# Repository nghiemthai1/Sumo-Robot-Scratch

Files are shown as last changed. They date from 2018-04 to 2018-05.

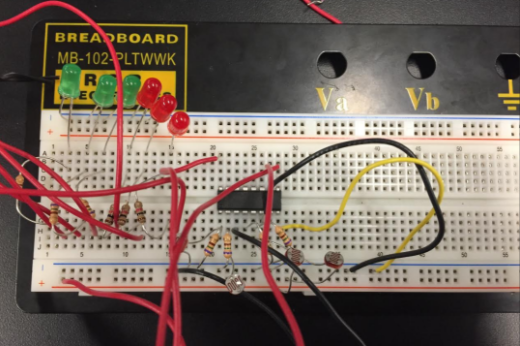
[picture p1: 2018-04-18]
Final Project Pictures/Multiplexer Schematic.png

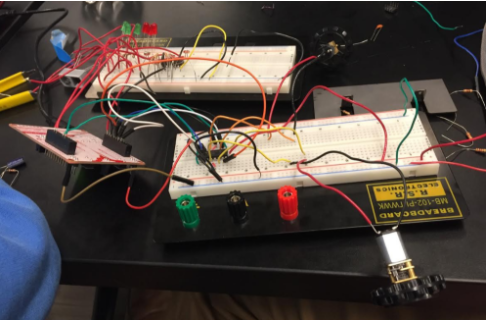
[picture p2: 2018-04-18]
Final Project Pictures/Multiplexer Schematic Overall.png

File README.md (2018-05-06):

# Sumo-Robot
### The SumoTest folder 
Contains the code for the robot. <br />
### The diptrace folder
Contains the schematic and pcb files.<br />
### The Final Project Pictures folder 
Contains figures in the final report.<br />
### The Parts List Emb.ods 
Contains a list of parts ordered, can only be opened with LibreOffice or other applications 
that can open .ods files.<br />
### The sumobot-final-project-report.pdf 
Is a pdf of - surprise- the sumobot final project report for Embedded Systems.<br />
blue

# Extra!
The sumo-bot is now implemented with a PID controller that follow an object at a desired distance!
### The PID_Controller folder contains the code and the pdf report of the project. 
Below is some graphic representation. <br />
 ezgif com-crop

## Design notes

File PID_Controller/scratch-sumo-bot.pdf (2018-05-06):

– ECE 09.321: Systems and Controls –

## Scratch Sumo-Bot: Tracking a Moving Object

Thai Nghiem, Russell Binaco Section 3

May 6, 2018

## 1 Abstract

## 2 Introduction

## 3 Standards And Constraints

Standards and constraints are regulations and limitations surrounding a project. Taking standards into consideration before designing the sumo-bot plays an important role in making the second-order design decisions and determining the success of the system.

### 3.1 Standards

Since the secondary purpose of the project is to compete in the Annual Rowan Prof Bots competition, the sumo-bot strictly follows the rules of competition. According to the rules, the design constraints of the bot are:

- The robot must have maximum dimensions of 10cm wide and 10cm long.
- The robot must have a mass no greater than 500g
- Robots must be self-impelled and self-controlled

All design choices must consider and fall within these parameters. The full competition ruleset can be found here (https://sumo.rowanieee.org/)

### 3.2 Constraints

Many minor constraints have to be taken into considerations when building this sumobot object follower, such as the stability, price, motor speed, distance, and available

Thai Nghiem, Russell Binaco | – ECE 09.321: Systems and Controls – | Section 3

hardware. First of all, the system must not have a high percent overshoot, since it might cause collision with the target object when there is a sudden change in position. Second of all, the total cost of the object follower must be relatively cheap (under 100 US Dollars), as there was very little money that was capable of being spent. Next, since the motor have a limited no-load speed of 400 RPM, the effect of the PID controller must not be too high, as it can make the bot go too slow. Lastly, it was a constraint to not use the Arduino processors in this project because it has a large library that can make the task seems trivial to implement.

## 4 Control Design

The task of following a moving object is inherently a Systems and Control task that requires feedback. The input to the system is a desired distance, so that distance must be transformed into a form that the microprocessor can use to compute motor speeds. In addition to system characterization, the PID controller should be tuned to a desired overshoot and steady-state error, as well as responsiveness. The ability of the system to reach a stable steady state should also be considered. This section of the report discusses the desired behavior of the system from a systems and control perspective, and section 6.1 discusses how the system behaved relative to these design considerations.

### 4.1 Characterizing Your System

The system is characterized by turning the distance between the robot and the target object into a digital value using the ADC converter. First, the output of the IR sensor(PRP220) was measured at varying distances from the sumo bot. The results are seen in the table in Figure 1 below.

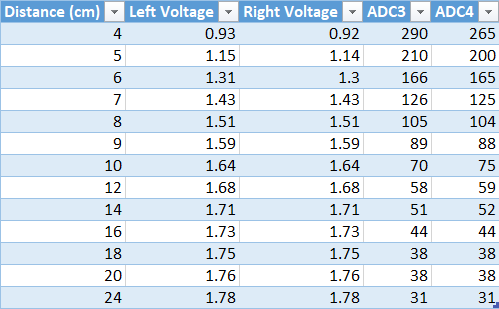
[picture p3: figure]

Figure 1: Characterization table.

Scratch Sumo-Bot: Tracking a Moving Object | 2

Thai Nghiem, Russell Binaco | – ECE 09.321: Systems and Controls – | Section 3

The results show the successful detection of an object within 30cm, a distance long enough to trail behind an object. The table is converted into a line graph as seen in Figure 2.

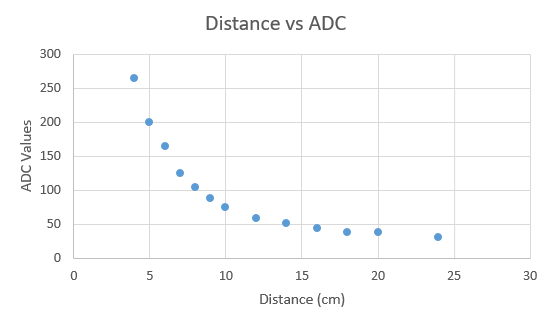
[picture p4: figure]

Figure 2: Distance vs. ADC graph.

This line is then divided into 3 pieces to create 3 piece-wise functions using equations (1) and (2) shown below. This is because an exponential decay graph is more computationally intensive to characterize than a straight line, and a piecewise function still provides a sufficient approximation of the characterized system. The implementation of the characterization code will be discussed later in Section 5.

m =

y2 − y1
x2 − x1

(1)

b = y1 − x1 · m | (2)

### 4.2 Design Goals

For a PID controller, design goals relate to the steady-state error, responsiveness (i.e. settling time) and overshoot of the system. When following an object, little to no overshoot is desired since overshoot could cause the sumo bot to collide with the object, which may not be desired. Settling time should be maximized and steady-state error should be minimized. Ultimately, the goal is to reach the desired distance from the object as quickly as possible, without overshooting that distance, and to minimize the oscillation and error at that distance.

### 4.3 Stability

By characterizing the system via the ADC readings from the sumo bot itself, the system is inherently stable. The only possible concern that could cause instability is a bad

Scratch Sumo-Bot: Tracking a Moving Object | 3

Thai Nghiem, Russell Binaco | – ECE 09.321: Systems and Controls – | Section 3

environment: for example, direct sunlight contains infrared light, which would cause the ADC readings to rise substantially and throwing off the characterization. Assuming the sumo bot is used indoors, only bad ADC readings from stray IR light or noise could cause a deviation in the system.

### 4.4 Control Loop Design

Figure 3 below shows the control loop for this system. Each portion of this loop was implemented as follows: First, the transformation from a desired distance to its equivalent ADC value was accomplished through the system characterization described above. The error signal comes from the difference between the average of the 10 most recent ADC readings and this characterized value. The implementation of the conversion from the error signal to a PWM duty cycle via the PID controller will be discussed in section 5.2. This process ultimately changes the position of the sumo bot, which is consistent with the initial set point also being a position.

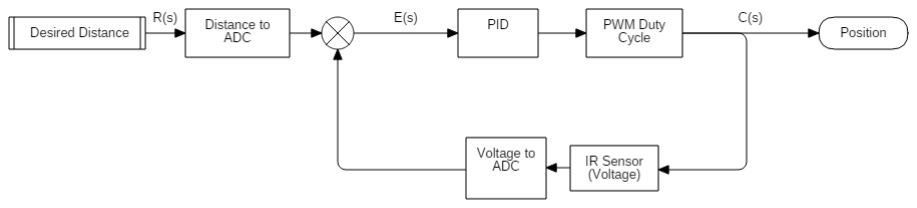
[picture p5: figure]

Figure 3: Block Diagram of PID System.

## 5 Design Discussion

### 5.1 Hardware

The sumo-bot was designed from scratch, with the advantage of being low cost, easy to adjust, and maintainable. The sumo-bot communicates with a MSP430F5529 using the built in ADC to read values from sensor and control two motors using an H-bridge. Each of the mentioned hardware parts of the robot will be discussed in detail in the following subsections.

### 5.1.1 Micro-controller

Choosing the right micro-controller was the first design choice to made, as it determines the efficiency of the system. The MSP430F5529 was decided on for various

Scratch Sumo-Bot: Tracking a Moving Object | 4

Thai Nghiem, Russell Binaco | – ECE 09.321: Systems and Controls – | Section 3

reasons. First of all, the micro-controller fits within the 10cm x 10cm dimension constraint given by the ProfBots competition. Also, the F5529 has 14 ADC channels (12 external at the device’s pins and 2 internal), which is enough for full functionality and communication with the sensors. The F5529 is also faster than most of the other boards including the G2 when making decisions off sensor readings. Finally, familiarity with the 5529 from previous projects and reusability of relevant code also played a large part in the microprocessor decision.

### 5.1.2 PCB

Three versions of the PCB was designed for the sumo-robot, but only the second version was used in the final product. In the last version, which can be seen from Figure 4 of the PCB, there are 4 main sections.

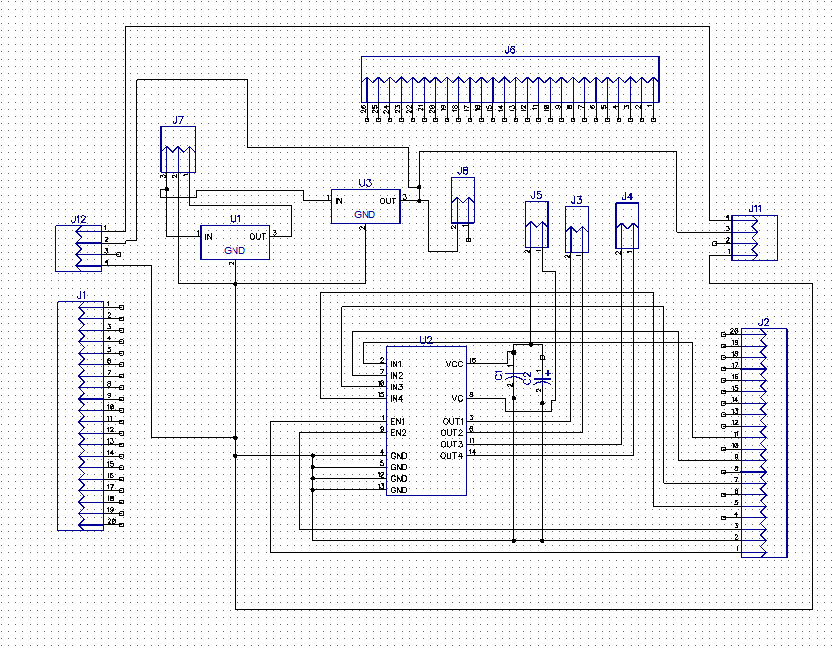
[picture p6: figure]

Figure 4: Schematic of breakout board used to power components.

The first section is the break-out board for the MSP430 to be mounted on. The second section is the H-bridge IC and the bulk and bypass capacitors that control the behavior of the 2 motors. The third section, which is on the top, is the two voltage regulators (5V and 3.3V). These are both used to supply power for the H-bridge and the MSP430. Finally, the last section, which is right next to the voltage regulator, is used for the IR sensors. In this section, the holes for the IR sensors are not connected to the pins of the MSP430, as to allow changes when actually building the robot. The layouts of the PCB can be seen in Figure 5

Scratch Sumo-Bot: Tracking a Moving Object | 5

Thai Nghiem, Russell Binaco | – ECE 09.321: Systems and Controls – | Section 3

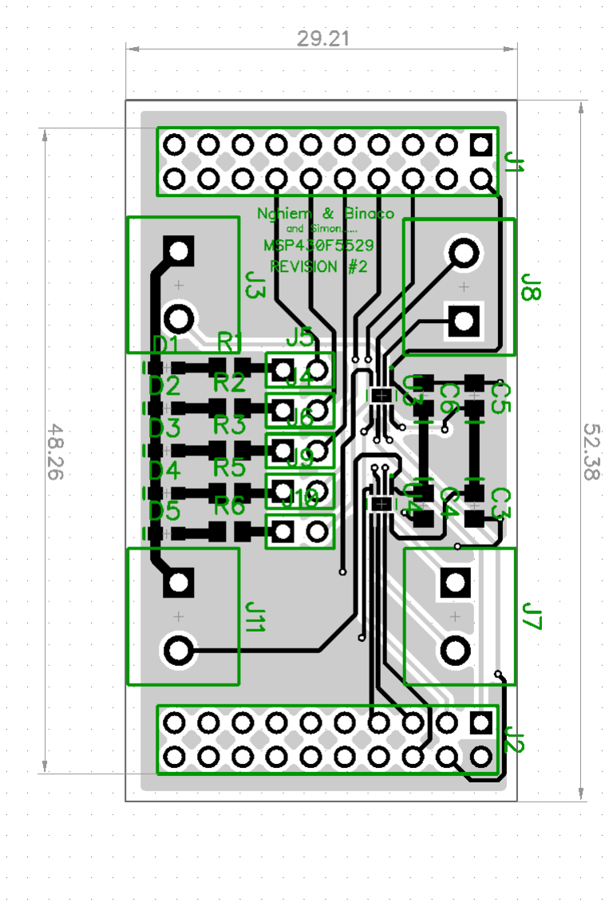
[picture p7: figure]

Figure 5: PCB Layouts of the final product.

### 5.1.3 Housing

The next step was to design the chassis and board housing in Solidworks, to be then 3-D printed. The chassiss design is based off the Zumo 32U Prime kit sumobot. The adjustments made are to optimize the specific motors chosen and adding in additional through holes for the plow and board attachment. The models are shown below in Figure 7.

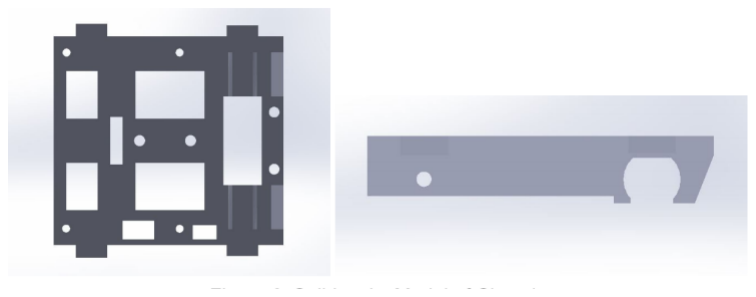
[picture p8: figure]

Figure 6: 3D Model of the Housing

Scratch Sumo-Bot: Tracking a Moving Object | 6

Thai Nghiem, Russell Binaco | – ECE 09.321: Systems and Controls – | Section 3

The next step was to take the 3-D design and import it to the Ultimaker Cura Studio to be 3-D printed. The design took approximately 8 hours to print on print speed setting of 0.1 and infill of 50

### 5.1.4 Sensors

There were many challenges when finally implementing the sensor design of the scratch sumo bot. Initially, the infrared sensor (TSSP4056) picked out needed a casing to be more accurate. However, it did not fit as well into the mechanical design of the bot, and the team was not satisfied with the performance of the TSSP4056. Upon further research of the old sumo bots used as references, the PRP220 IR sensor was discovered. The sensor was tested by the built circuit as seen in Figure ??. This circuit is then implemented in a ProtoBoard. The sensor was able to detect changes between black and white as well as objects within 30cm very well.

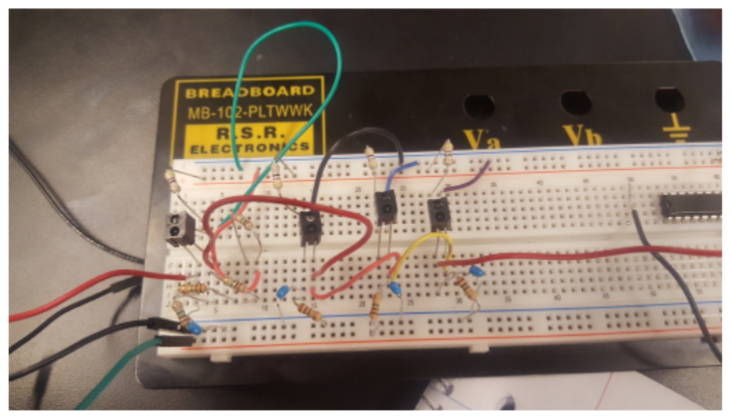
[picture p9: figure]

Figure 7: Picture of breadboard test setup with IR sensors.

### 5.1.5 Control Diagram

A general overview of the functioning of the system can be seen in Figure 8. A 12V energy sources powers a 5V regulator, a 3.3V regulator, and the motors that are connected to the H-Bridge. The 3.3V regulator powers the infrared LEDs, which reflect off surfaces and into the nearby infrared sensors. The sensors send an analog voltage back into the MSP430, which converts it into an analog signal and compares it thresholds that drive the logic of the H-bridge. Finally, the H-bridge controls the motors of the sumobot. The code is explained more in detail in the design approach.

Scratch Sumo-Bot: Tracking a Moving Object | 7

Thai Nghiem, Russell Binaco | – ECE 09.321: Systems and Controls – | Section 3

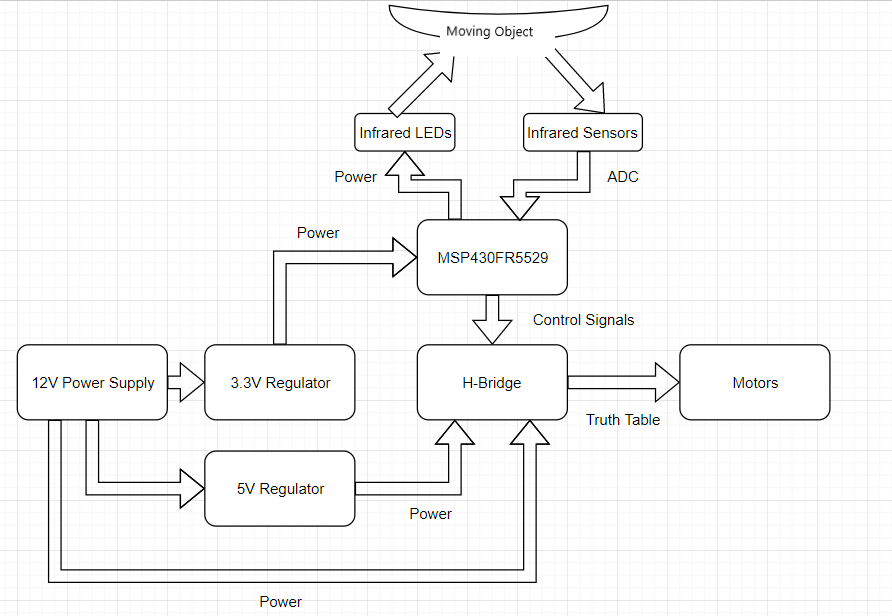
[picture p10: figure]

Figure 8: Diagram of the sumo-bot as a whole.

### 5.2 Software

### 5.2.1 ADC12

The analog to digital (ADC) conversion plays an important role in the design of the sumobot. The sensors output a voltage depending the distance of objects in front of them. The ADC interrupt was placed in a while loop so the microprocessor is constantly checking the voltage readings from the sensors in order to make decisions based on the inputs.
The code for the ADC conversion that is used in sensing the environment can be seen below (with the ADC initialization omitted).

/ ∗
∗ Enable the ADC c o n v e rt e r t o s t a r t sensing the envi ronment
∗ Thi s f u n c t i o n i s c a l l e d i n main
∗ /
v o i d sensing ( v o i d )
{
ADC12CTL0 |= ADC12ENC; | / / ADC12 enabled
ADC12CTL0 |= ADC12SC; | / / S t a r t sampling / con ve r sion
b i s S R r e g i s t e r ( GIE ) ; | / / LPM0, ADC12 ISR w i l l f o r c e e x i t

}

### 5.2.2 PWM - Motors Speed

Pulse width modulation is used to control the speed of each motor on the sumo-bot. In order for this to be achieved two PWM signals were output to Pin 1.4 and Pin 2.4.

Scratch Sumo-Bot: Tracking a Moving Object | 8

Thai Nghiem, Russell Binaco | – ECE 09.321: Systems and Controls – | Section 3

Pin 1.4 controlled the speed of the right motor and Pin 2.4 controlled the speed of the left motor. TA0CC3 was used to control the right motor and TA2CCR1 was used to control the left motor. The PWM cycle is controlled using values 0-999. Setting TA0CC3/TA2CCR1 = 0 will produce a duty cycle of 0% and setting TA0CC3/TA2CCR1 = 999 will produce a duty cycle of 100%.
The code to set the speed of motor using PWM can be seen below (with the PWM initialization being omitted).

/ ∗
∗ Thi s f u n c t i o n s et the PWM value of the
∗ two motors , hence c o n t r o l t h e i r speed ∗ /
v o i d setMoto r ( i n t l e f t , i n t r i g h t )
{
i f ( r i g h t < 0 ) / / Backwards , clo c k−wise
{
| P2OUT |= BIT5 ; / / Sets d i r e c t i o n f o r H−b r i d g e
TA0CCR3 = ( l e f t ∗ −1); / / Speed of the motor CCR/1000 }
e l s e i f ( r i g h t == 0 ) / / st o p p i n g
{
| TA0CCR3 = 0;
}
e l s e / / Forwards , counte r clo c k−wise
{
| P2OUT &= ˜ BIT5 ; / / Sets d i r e c t i o n f o r H−b r i d g e TA0CCR3 = l e f t ; / / Speed of the motor CCR/1000

}
| | [ same code i s done f o r the l e f t ]

}

### 5.2.3 Characterization

As previously discussed, the distance between the sumo-bot and the target object is characterized into ADC value as to control the PWM of the 2 motors. This is done by turning the line graph in Figure 2 into 3 straight line graphs, as shown in Figure 9. The first graph represents the ADC value versus a distance from 0 to 7 cm. The second graph represents the ADC value versus a distance from 7 to 12 cm. The last graph represents the ADC value versus a distance from 12 to 30 cm.

Scratch Sumo-Bot: Tracking a Moving Object | 9

Thai Nghiem, Russell Binaco | – ECE 09.321: Systems and Controls – | Section 3

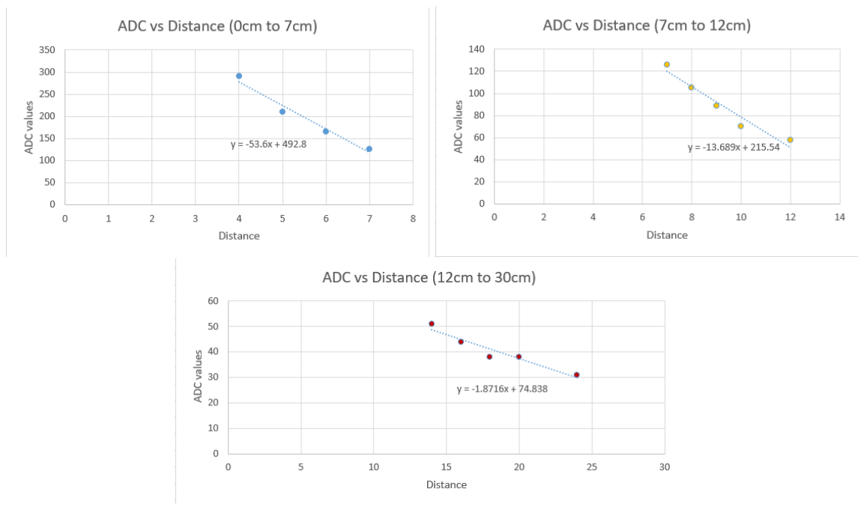
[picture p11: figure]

Figure 9: 3 straight line graphs derived from 1 curved line.

These graphs are then utilized to create 3 piecewise functions using Equation (1) and (2). The 3 functions is implemented in the code as follows to give us the equivalent ADC values.

/ ∗
∗ C h a r a ct e r i z at i o n code f o r the system
∗ Conve rt the d e s i r e d d i st a n c e t o ADC value ∗ Using piece−wise f u n c t i o n s
∗ /
v o i d distToADC ( i n t d i st a n c e ){
/ / 0cm t o 7cm range
i f ( d i st a n c e >= 0 && d i st a n c e <= 7 ){
ad c out = d i st a n c e ∗−53.6 + 4 9 2. 8;
/ / 7cm t o 12cm range
} e l s e i f ( d i st a n c e > 7 && d i st a n c e <= 12 ){ ad c out = d i st a n c e ∗−13.689 + 215.54;
/ / 12cm t o 30cm range
} e l s e i f ( d i st a n c e > 12 && d i st a n c e <= 30 ){ ad c out = d i st a n c e ∗−1.8716 + 74.838;
}
/ / D ef a u lt value
e l s e {
ad c out = 290;
}
}
Scratch Sumo-Bot: Tracking a Moving Object | 10

Thai Nghiem, Russell Binaco | – ECE 09.321: Systems and Controls – | Section 3

Hence, when the user input a desired distance of 5 cm after the target object, the above function will assign it into the first if-statement, and produce an equivalent ADC value that will control the speed of the 2 motors.

### 5.2.4 PID Controller

/ ∗
∗ P r o p o r t i o n a l − I n t e g r a l − D e r i v a t i v e C o n t r o l l e r of the r o b ot ∗ I s c a l l e d i n the I n t e r r u p t
∗ /
v o i d updatePID ( v o i d ){
/ / C a l c u l at i n g the E r r o r term
e r r o r 3P r e v = e r r o r 3 ; / / R ight motor e r r o r 4P r e v = e r r o r 4 ; / / L e f t motor e r r o r 3 = d e s i r e d − adc3 ;
e r r o r 4 = d e s i r e d − adc4 ;

/ / C a l c u l at i n g the P r o p o r t i o n a l term
p r o p o r t i o n a l 3 = Kp ∗ e r r o r 3 ; / / R ight motor p r o p o r t i o n a l 4 = Kp ∗ e r r o r 4 ; / / L e f t motor

/ / C a l c u l at i n g the D e r i v a t i v e term
d e r i v a t i v e 3 = Kd ∗ ( e r ro r3P re v−e r r o r 3 ) ; / / R ight motor d e r i v a t i v e 4 = Kd ∗ ( e r ro r4P re v−e r r o r 4 ) ; / / Ledt motor

/ / C a l c u l at i n g the accumulato r f o r the E r r o r term accumulato r3 = accumulato r3 += e r r o r 3 ;
accumulato r4 = accumulato r4 += e r r o r 4 ;

/ / Capping accumulato r value s
i f ( accumulato r3 >50){ / / R ight motor
| accumulato r3 = 50;
} e l s e i f ( accumulato r3 <−50){
| accumulato r3 = −50;
}
i f ( accumulato r4 >50){ | / / L e f t motor
| accumulato r4 = 50;
} e l s e i f ( accumulato r4 <−50){
| accumulato r4 = −50;
}

/ / C a l c u l at i n g the I n t e g r a l term
i n t e g r a l 3 = Ki ∗ accumulato r3 ; / / R ight motor i n t e g r a l 4 = Ki ∗ accumulato r4 ; / / L e f t motor
Scratch Sumo-Bot: Tracking a Moving Object | 11

Thai Nghiem, Russell Binaco | – ECE 09.321: Systems and Controls – | Section 3

/ / Adding the P r o p o r t i o n a l − I n t e g r a l − D e r i v a t i v e temrs / / up t o c r e at e the PID c o n t r o l l e r
pid3 = p r o p o r t i o n a l 3 + i n t e g r a l 3 −d e r i v a t i v e 3 ;
pid4 = p r o p o r t i o n a l 4 + i n t e g r a l 4 −d e r i v a t i v e 4 ;

/ / c o n v e rt p i d range t o PWM range setScaledMoto r ( pid3 , pid4 ) ;
}

## 6 Results and Conclusions

### 6.1 System Behavior

### 6.1.1 Proportional Control

### 6.1.2 PID Control

### 6.1.3 Steady State

### 6.2 Conclusions

### 6.3 Contributions

The team always work together through the process of making the sumo-bot object follower. However, each member has his own specialty and can be breakdown into different categories and be seen in the following table.

Thai Nghiem | Russell Binaco
Project Proposal Hardware Implementation Characterization | PID Controller Research Software Implementation Battery Sponsor

Acknowledgement: The authors would like to thank Dr. Al-Quzwini, Russell Trafford and Simonas Bublis for giving us advice and support throughout the project.

Scratch Sumo-Bot: Tracking a Moving Object | 12

Thai Nghiem, Russell Binaco | – ECE 09.321: Systems and Controls – | Section 3

## 7 Appendix A

## References

[1] Nise, Norman S. Control Systems Engineering. Wiley, 2011. Print.

## 8 Appendix B

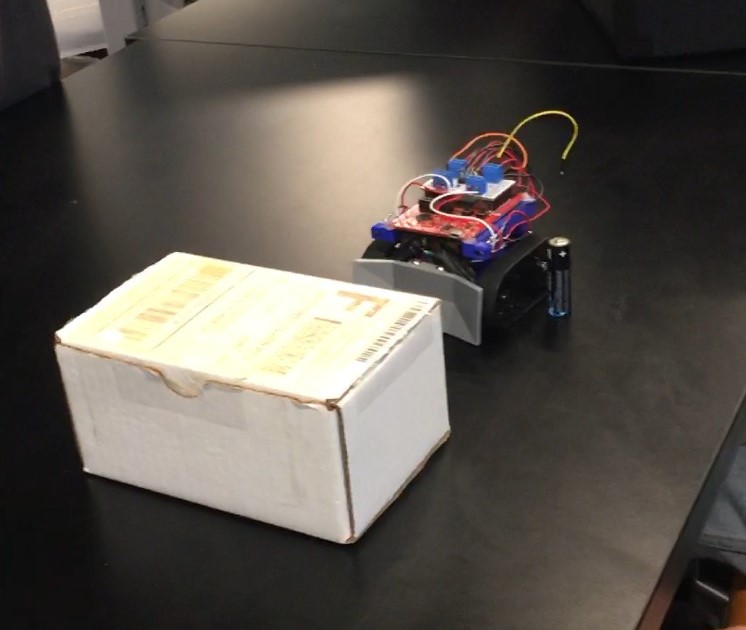
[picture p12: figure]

Figure 10: Sumo-bot and its object

Scratch Sumo-Bot: Tracking a Moving Object | 13

Thai Nghiem, Russell Binaco | – ECE 09.321: Systems and Controls – | Section 3

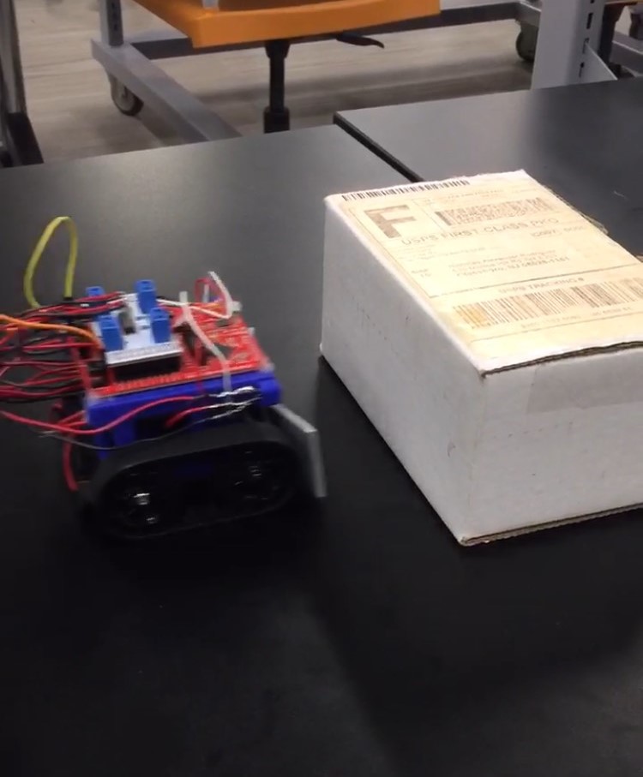
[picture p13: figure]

Figure 11: Sumo-bot and its object.

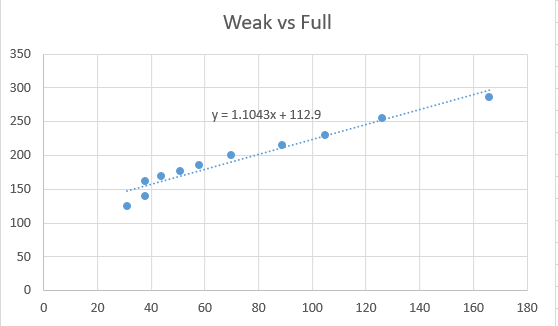
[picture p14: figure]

Figure 12: ADC value between low battery and full battery.

Scratch Sumo-Bot: Tracking a Moving Object | 14

Thai Nghiem, Russell Binaco | – ECE 09.321: Systems and Controls – | Section 3
1 | # i n c l u d e <msp430 . h>
2 | / / f o r a ve raging ADC value s
3 | i n t adc3 = 0;
4 | i n t adc4 = 0;
5 | i n t buf3 [ 1 0 ] ;
6 | i n t buf4 [ 1 0 ] ;
7 | unsigned i n t inde x ;

8
9 | i n t Kp=3;
10 | i n t Kd=0;
11 | i n t Ki =0;
12 | i n t e r r o r 3 = 0;
13 | i n t e r r o r 4 = 0;
14 | i n t e r r o r 3P r e v = 0;
15 | i n t e r r o r 4P r e v = 0;
16 | i n t p r o p o r t i o n a l 3 = 0;
17 | i n t p r o p o r t i o n a l 4 = 0;
18 | i n t d e r i v a t i v e 3 = 0;
19 | i n t d e r i v a t i v e 4 = 0;
20 | i n t accumulato r3 = 0;
21 | i n t accumulato r4 = 0;
22 | i n t i n t e g r a l 3 = 0;
23 | i n t i n t e g r a l 4 = 0;
24 | i n t pid3 = 0;
25 | i n t pid4 = 0;
26 | i n t tempLeft = 0;
27 | i n t tempRight = 0;
28 | i n t ad c out =0;
29 | i n t s c a l e v a l u e = 8;

30
31 | i n t c o n t r o l t y p e = 0;
32 | i n t f l a g = 0;
33 | i n t d e s i r e d = 0; / /ADC value
34 | v o i d PWMInit ( v o i d ) ;
35 | v o i d sensing ( v o i d ) ;
36 | v o i d s t a r t i n g ( v o i d ) ;
37 | v o i d setMoto r ( ) ;
38 | v o i d ADCInit ( v o i d ) ;
39 | v o i d updatePID ( v o i d ) ;
40 | v o i d distToADC ( i n t d i st a n c e ) ;
41 | v o i d setScaledMoto r ( i n t l e f t , i n t r i g h t ) ;
42 | v o i d p i n I n i t ( v o i d ) ;

43

44
45 | /∗ ∗
46 | ∗ main . c
47 | ∗/
48 | i n t main ( v o i d )
49 | {
50 | / / Stop watchdog t im e r
51 | WDTCTL = WDTPW | WDTHOLD;

52
53 | / / I n i t i a l i z a t i o n
54 | p i n I n i t ( ) ;
55 | PWMInit ( ) ;
56 | ADCInit ( ) ;

57

Scratch Sumo-Bot: Tracking a Moving Object | 15

Thai Nghiem, Russell Binaco | – ECE 09.321: Systems and Controls – | Section 3
58 | / / Reset the speed of both motors
59 | setMoto r ( 0 , 0 ) ;

60
61 | /∗
62 | ∗ | Compute d e s i r e d value i n ADC
63 | ∗ | Max : 200 ( c l o s e st )
64 | ∗ | Min : 100 ( f u r t h e s t
65 | ∗
66 | ∗ | d e s i r e d = 200;
67 | ∗/

68
69 | / / Desi red t r a i l i n g d i st a n c e
70 | i n t d i st a n c e = 5; / / i n c e nt im et e r s
71 | distToADC ( d i st a n c e ) ; / / Di stan ce t o ADC value

72
73 | / / Sumo−bot c o n st a nt l y sense the envi ronment
74 | w h i l e ( 1 ) / / i n i f i t e loop
75 | {
76 | sensing ( ) ;
77 | }
78 | }

79

80
81 | v o i d s t a r t i n g ( v o i d )
82 | {
83 | sensing ( ) ;
84 | }

85
86 | /∗
87 | ∗ Enable the ADC c o n v e rt e r t o s t a r t sensing the envi ronment
88 | ∗ Thi s f u n c t i o n i s c a l l e d i n main
89 | ∗/
90 | v o i d sensing ( v o i d )
91 | {
92 | ADC12CTL0 |= ADC12ENC; | / / ADC12 enabled
93 | ADC12CTL0 |= ADC12SC; | / / S t a r t sampling / con ve r sion
94 | b i s S R r e g i s t e r ( GIE ) ; | / / LPM0, ADC12 ISR w i l l f o r c e e x i t

95
96 }

97
98 | /∗
99 | ∗ P r o p o r t i o n a l − I n t e g r a l − D e r i v a t i v e C o n t r o l l e r of the r o b ot
100 | ∗ I s c a l l e d i n the I n t e r r u p t
101 | ∗/
102 | v o i d updatePID ( v o i d ) {
103 | / / C a l c u l at i n g the E r r o r term
104 | e r r o r 3P r e v = e r r o r 3 ; / / R ight motor
105 | e r r o r 4P r e v = e r r o r 4 ; / / L e f t motor
106 | e r r o r 3 = d e s i r e d − adc3 ;
107 | e r r o r 4 = d e s i r e d − adc4 ;

108
109 | / / C a l c u l at i n g the P r o p o r t i o n a l term
110 | p r o p o r t i o n a l 3 = Kp ∗ e r r o r 3 ; / / R ight motor
111 | p r o p o r t i o n a l 4 = Kp ∗ e r r o r 4 ; / / L e f t motor

112
113 | / / C a l c u l at i n g the D e r i v a t i v e term
114 | d e r i v a t i v e 3 = Kd ∗ ( e r ro r3P re v−e r r o r 3 ) ; / / R ight motor
Scratch Sumo-Bot: Tracking a Moving Object | 16

Thai Nghiem, Russell Binaco | – ECE 09.321: Systems and Controls – | Section 3
115 | d e r i v a t i v e 4 = Kd ∗ ( e r ro r4P re v−e r r o r 4 ) ; / / Ledt motor

116
117 | / / C a l c u l at i n g the accumulato r f o r the E r r o r term
118 | accumulato r3 = accumulato r3 += e r r o r 3 ;
119 | accumulato r4 = accumulato r4 += e r r o r 4 ;

120
121 | / / Capping accumulato r value s
122 | i f ( accumulato r3 >50){ / / R ight motor
123 | accumulato r3 = 50;
124 | } e l s e i f ( accumulato r3 <−50){
125 | accumulato r3 = −50;
126 | }

127
128 | i f ( accumulato r4 >50){ | / / L e f t motor
129 | accumulato r4 = 50;
130 | } e l s e i f ( accumulato r4 <−50){
131 | accumulato r4 = −50;
132 | }

133
134 | / / C a l c u l at i n g the I n t e g r a l term
135 | i n t e g r a l 3 = Ki ∗ accumulato r3 ; / / R ight motor
136 | i n t e g r a l 4 = Ki ∗ accumulato r4 ; / / L e f t motor

137
138 | / / Adding the P r o p o r t i o n a l − I n t e g r a l − D e r i v a t i v e temrs
139 | / / up t o c r e at e the PID c o n t r o l l e r
140 | pid3 = p r o p o r t i o n a l 3 + i n t e g r a l 3 −d e r i v a t i v e 3 ;
141 | pid4 = p r o p o r t i o n a l 4 + i n t e g r a l 4 −d e r i v a t i v e 4 ;

142
143 | / / c o n v e rt p i d range t o PWM range
144 | setScaledMoto r ( pid3 , pid4 ) ;
145 | }

146
147 | /∗
148 | ∗ Thi s f u n c t i o n s ca le the PWM range , s in ce the l e f t motor i s
149 | ∗ s l i g h t l y st r o n g e r than the r i g h t motor , making the r o b ot
150 | ∗ st e e r r i g h t .
151 | ∗/
152 | v o i d setScaledMoto r ( i n t l e f t , i n t r i g h t ) {
153 | / / l e f t l i m i t −999 t o 999
154 | / / r i g h t l i m i t −870 t o 870
155 | / / expected range −200 t o 200
156 | tempLeft = ( l e f t ∗5/ 2 ) ∗ s c a l e v a l u e ;
157 | tempRight = ( ( r i g h t ∗9 ) / 4 ) ∗ s c a l e v a l u e ;

158
159 | / / 30 i s minimum value ( f u r t h e s t )
160 | i f ( tempLeft < 30 && tempLeft > 0 ) {
161 | tempLeft = 30;
162 | }
163 | i f ( tempRight < 30 && tempRight > 0 ) {
164 | tempRight = 30;
165 | }

166
167 | i f ( tempLeft > −30 && tempLeft < 0 ) {
168 | tempLeft = −30;
169 | }
170 | i f ( tempRight > −30 && tempRight < 0 ) {
171 | tempRight = −30;
Scratch Sumo-Bot: Tracking a Moving Object | 17

Thai Nghiem, Russell Binaco | – ECE 09.321: Systems and Controls – | Section 3
172 | }
173 | / / 999 i s maximum value ( c l o s e st )
174 | i f ( tempLeft< −999){
175 | | tempLeft = −999;
176 | }
177 | i f ( tempRight< −999){
178 | tempRight = −999;
179 | }

180
181 | i f ( tempLeft >999){
182 | | tempLeft = 999;
183 | }
184 | i f ( tempRight >870){
185 | | tempRight = 870;
186 | }
187 | / / | R ight | L e f t
188 | setMoto r ( tempLeft , tempRight ) ;

189
190 }

191
192 | /∗
193 | ∗ Thi s f u n c t i o n s et the PWM value of the
194 | ∗ two motors , hence c o n t r o l t h e i r speed
195 | ∗/
196 | v o i d setMoto r ( i n t l e f t , i n t r i g h t )
197 | {
198 | i f ( r i g h t < 0 ) / / Backwards , clo c k−wise
199 | {
200 | P2OUT |= BIT5 ; / / Sets d i r e c t i o n f o r H−b r i d g e
201 | TA0CCR3 = ( l e f t ∗ −1) ; / / Speed of the motor CCR/1000
202 | }
203 | e l s e i f ( r i g h t == 0 ) / / st o p p i n g
204 | {
205 | | TA0CCR3 = 0;
206 | }
207 | e l s e / / Forwards , counte r clo c k−wise
208 | {
209 | P2OUT &= ˜ BIT5 ; / / Sets d i r e c t i o n f o r H−b r i d g e
210 | TA0CCR3 = l e f t ; / / Speed of the motor CCR/1000
211 | }

212
213 | i f ( l e f t < 0 )
214 | {
215 | | P1OUT |= BIT5 ;
216 | TA2CCR1 = ( r i g h t ∗ −1) ;
217 | }
218 | e l s e i f ( l e f t == 0 )
219 | {
220 | | TA2CCR1 = 0;
221 | }
222 | e l s e / / fo rwa rds , clo c k−wise
223 | {
224 | | P1OUT &= ˜ BIT5 ;
225 | | TA2CCR1 = r i g h t ;
226 | }
227 | }

228

Scratch Sumo-Bot: Tracking a Moving Object | 18

Thai Nghiem, Russell Binaco | – ECE 09.321: Systems and Controls – | Section 3
229 | /∗
230 | ∗ C h a r a ct e r i z at i o n code f o r the system
231 | ∗ Conve rt the d e s i r e d d i st a n c e t o ADC value
232 | ∗ Using piece−wise f u n c t i o n s
233 | ∗/
234 | v o i d distToADC ( i n t d i st a n c e ) {
235 | / / 0cm t o 7cm range
236 | i f ( d i st a n c e >= 0 && d i st a n c e <= 7 ) {
237 | ad c out = d i st a n c e ∗−53.6 + 4 9 2. 8;
238 | / / 7cm t o 12cm range
239 | } e l s e i f ( d i st a n c e > 7 && d i st a n c e <= 12 ){
240 | ad c out = d i st a n c e ∗−13.689 + 215.54;
241 | / / 12cm t o 30cm range
242 | } e l s e i f ( d i st a n c e > 12 && d i st a n c e | <= 30 ){
243 | ad c out = d i st a n c e ∗−1.8716 + 74.838;
244 | }
245 | / / D ef a u lt value
246 | e l s e {
247 | ad c out = 290;
248 | }
249 | }
250 | v o i d p i n I n i t ( v o i d ) {
251 | P2DIR |= BIT0 ; | / / Pin 2.0 i n i t i a l i z a t i o n
252 | P2OUT |= BIT0 ;

253
254 | P2DIR |= BIT2 ; | / / Pin 2.2 i n i t i a l i z a t i o n
255 | P2OUT |= BIT2 ;

256
257 | P2DIR |= BIT5 ;
258 | P1DIR |= BIT5 ;

259
260 | P1SEL =0; / / S e l e ct GPIO o pt i o n
261 | P1DIR |= BIT0 ; / / s et P o rt 1.0 o ut p ut −−−LED
262 | P1OUT &= ˜ BIT0 ; | / / LED OFF

263
264 | P4SEL =0; / / S e l e ct GPIO o pt i o n
265 | P4DIR |= BIT7 ; / / s et P o rt 4.7 o ut p ut −−−LED
266 | P4OUT &= ˜ BIT7 ; | / / LED OFF

267
268 | P1DIR &= ˜ ( BIT1 ) ; / / s et P o rt 1.1 i n p ut −−− pushbutton
269 | P1REN|= BIT1 ; / / enable p u l l −up / p u l l −down r e s i s t o r on
270 | P1OUT|= BIT1 ; / / choose the p u l l −up r e s i s t o r

271
272 | P1IE |= BIT1 ; / / enable the i n t e r r u p t on P o rt 1.1
273 | P1IES |= BIT1 ; / / s et as f a l l i n g edge
274 | P1IFG &= ˜ ( BIT1 ) ; / / c l e a r i n t e r r u p t f l a g
275 | }
276 | v o i d PWMInit ( v o i d )
277 | {
278 | P1DIR |= BIT4 ; | / / I n i t i a l i z e PWM t o o ut p ut on P1. 4
279 | P1SEL |= BIT4 ;

280
281 | P2DIR |= BIT4 ; | / / I n i t i a l i z e PWM t o o ut p ut on P2. 4
282 | P2SEL |= BIT4 ;

283
284 | TA0CCR0 =1000−1;
285 | TA2CCR0 =1000−1;
Scratch Sumo-Bot: Tracking a Moving Object | 19

Thai Nghiem, Russell Binaco | – ECE 09.321: Systems and Controls – | Section 3
286 | TA0CCTL3 =OUTMOD 7;
287 | TA0CCR3 =999;
288 | TA2CCTL1 =OUTMOD 7;
289 | TA2CCR1 = 999;
290 | TA0CTL = TASSEL 2 + MC 1 + TACLR;
291 | TA2CTL = TASSEL 2 + MC 1 + TACLR;
292 | }

293
294 | v o i d ADCInit ( v o i d )
295 | {
296 | ADC12CTL0 = ADC12ON+ADC12MSC+ADC12SHT02; / / Turn on ADC12, s et sampling
time
297 | ADC12CTL1 = ADC12SHP+ADC12CONSEQ 1; | / / Use sampling t ime r , s i n g l e
sequence
298 | ADC12MCTL0 = ADC12INCH 0 ; | / / r e f +=AVcc , channel = A0
299 | ADC12MCTL1 = ADC12INCH 1 ; | / / r e f +=AVcc , channel = A1
300 | ADC12MCTL2 = ADC12INCH 2 ; | / / r e f +=AVcc , channel = A2
301 | ADC12MCTL3 = ADC12INCH 3 ;
302 | ADC12MCTL4 = ADC12INCH 4 + ADC12EOS; | / / r e f +=AVcc , channel = A3 ,
end seq .
303 | ADC12IE = 0x10 ; | / / Enable ADC12IFG. 3
304 | ADC12CTL0 |= ADC12ENC; | / / Enable con ve r sion s
305 | /∗ Sets ADC Pin t o NOT GPIO∗/
306 | P6SEL |= BIT1 + BIT2 + BIT3 + BIT4 ; | / / P6. 0 ADC
o pt i o n s e l e c t
307 | P6DIR &= ˜ ( BIT1 + BIT2 + BIT3 + BIT4 ) ;
308 | P6REN |= BIT1 + BIT2 + BIT3 + BIT4 ;
309 | P6OUT &= ˜ ( BIT1 + BIT2 + BIT3 + BIT4 ) ;
310 | ADC12CTL0 |= ADC12ENC;
311 | ADC12CTL0 |= ADC12SC;
312 | }

313
314 | # i f d ef i n e d ( TI COMPILER VERSION ) | | d ef i n e d ( IAR SYSTEMS ICC )
315 | #pragma v e ct o r = ADC12 VECTOR
316 | i n t e r r u p t v o i d ADC12 ISR ( v o i d )
317 | # e l i f d ef i n e d ( GNUC )
318 | v o i d | a t t r i b u t e | ( ( i n t e r r u p t (ADC12 VECTOR ) ) ) ADC12 ISR ( v o i d )
319 | #e l s e
320 | # e r r o r Compile r not suppo rted !
321 | # e n d if
322 | {

323
324 | sw it c h ( | e v e n i n r a n g e ( ADC12IV , 3 4 ) )
325 | {
326 | case | 0: break ; | / / Ve cto r | 0: | No i n t e r r u p t
327 | case | 2: break ; | / / Ve cto r | 2: | ADC o v e rf l ow
328 | case | 4: break ; | / / Ve cto r | 4: | ADC t im i n g
o v e rf l ow
329 | case | 6: break ; | / / Ve cto r | 6: | ADC12IFG0
330 | case | 8: break ; | / / Ve cto r | 8: | ADC12IFG1
331 | case 10: break ; | / / Ve cto r 10: | ADC12IFG2
332 | case 12: break ; | / / Ve cto r 12: | ADC12IFG3
333 | case 14:
334 | / / For eve ry 10 ADC samples , we use 1 f o r s t a b i l i t y of the system
335 | i f ( inde x < 10 ){ | / / adds new value t o a r r a y f o r average of 10
336 | buf3 [ inde x ] = ADC12MEM3; / / b u f f e r f o r r i g h t motor
337 | buf4 [ inde x ] = ADC12MEM4;
Scratch Sumo-Bot: Tracking a Moving Object | 20

Thai Nghiem, Russell Binaco | – ECE 09.321: Systems and Controls – | Section 3
338 | inde x ++;
339 | }
340 | e l s e { | / / computes average of 10 and t r a n sm it s value ; r e s et s a r r a y
inde x
341 | long average3 = 0;
342 | long average4 = 0;
343 | i n t i = 0;
344 | f o r ( i = 0; i < 10 ; i ++){
345 | average3 += buf3 [ i ] ;
346 | average4 += buf4 [ i ] ;
347 | }
348 | average3 /= 10;
349 | average4 /= 10;
350 | inde x =0;
351 | f l a g =1;
352 | / / −120 f o r F u l l vs Weak
353 | adc3 = average3 ; / / changes dut y c y c l e
354 | adc4 = average4 ; / / changes dut y c y c l e

355
356 | / / C a l l i n g the PID c o n t r o l l e r f u n c t i o n
357 | updatePID ( ) ;
358 | }

359
360 | b i c S R r e g i s t e r o n e x i t ( LPM0 bits ) ;
361 | break ; | / / Ve cto r 14: | ADC12IFG4
362 | case 16: break ; | / / Ve cto r 16: | ADC12IFG5
363 | case 18: break ; | / / Ve cto r 18: | ADC12IFG6
364 | case 20: break ; | / / Ve cto r 20: | ADC12IFG7
365 | case 22: break ; | / / Ve cto r 22: | ADC12IFG8
366 | case 24: break ; | / / Ve cto r 24: | ADC12IFG9
367 | case 26: break ; | / / Ve cto r 26: | ADC12IFG10
368 | case 28: break ; | / / Ve cto r 28: | ADC12IFG11
369 | case 30: break ; | / / Ve cto r 30: | ADC12IFG12
370 | case 32: break ; | / / Ve cto r 32: | ADC12IFG13
371 | case 34: break ; | / / Ve cto r 34: | ADC12IFG14
372 | d e f a u l t : b reak ;
373 | }
374 | }

375
376 | /∗
377 | ∗ Button I n t e r r u p t t h a t c o n t r o l the C o n t r o l l e r Type of the r o b ot
378 | ∗ There a re 4 modes i n t o t a l : o n l y P r o p o rt i o n a l , P r o p o rt i o n a l −I n t e g r a l ,
379 | ∗ P r o p o rt i o n a l −D e r i v at i v e , and a l l P r o p o rt i o n a l −I n t e g r a l −D e r i v a t i v e
380 | ∗/
381 | #pragma v e ct o r =PORT1 VECTOR
382 | i n t e r r u p t v o i d PORT 1 ( v o i d )
383 | {
384 | P1IE &= ˜ BIT1 ; / / Di sable i n t e r r u p t

385
386 | / / Debounce 1
387 | d e l a y c y c l e s ( 1 ) ;

388
389 | / / Debounce 2
390 | TA1CTL = TASSEL 1 + MC 1 + ID 1 ; / / Set up Timer A, Count up , d i v i d e r 2
391 | TA1CCTL0 = 0x10 ; / / Set up compare mode f o r CCTL
392 | TA1CCR0 = 2000; / / D u r at i o n at which the i n t e r r u p t i s d i s a b l e
393 | / / D u r at i o n 2000/16kHz = 1/8 sec .
Scratch Sumo-Bot: Tracking a Moving Object | 21

Thai Nghiem, Russell Binaco | – ECE 09.321: Systems and Controls – | Section 3
394 | P1IFG &= ˜ ( BIT1 ) ; / / Clea r f l a g

395
396 | / / Loop back t o c o n t r o l t ype 0
397 | i f ( c o n t r o l t y p e > 3 ) {
398 | c o n t r o l t y p e = 0;
399 | }

400
401 | sw it c h ( c o n t r o l t y p e ) {
402 | case 0: / / Only PI
403 | P4OUT |= BIT7 ; / / Turn 4.7 on f o r 01
404 | P1OUT &= ˜ BIT0 ; / / Turn 1.0 on
405 | Ki =1;
406 | s c a l e v a l u e = 5;
407 | break ;
408 | case 1: / / PD
409 | P1OUT |= BIT0 ; / / Turn 1.0 on f o r 10
410 | P4OUT &= ˜ BIT7 ; / / Turn 4.7 o f f
411 | Ki = 0;
412 | Kd = 1;
413 | s c a l e v a l u e = 8;
414 | break ;
415 | case 2: / / PID
416 | P4OUT |= BIT7 ; / / Turn 4.7 on f o r 11
417 | P1OUT |= BIT0 ; / / Turn 1.0 on f o r
418 | Ki = 1;
419 | Kd = 1;
420 | s c a l e v a l u e = 1;
421 | break ;
422 | case 3: / / Only P
423 | P4OUT &= ˜ BIT7 ; / / Turn 4.7 on f o r 11
424 | P1OUT &= ˜ BIT0 ; / / Turn 1.0 on f o r
425 | Ki = 0;
426 | Kd = 0;
427 | s c a l e v a l u e = 8;
428 | break ;
429 | d e f a u l t :
430 | break ;
431 | }
432 | c o n t r o l t y p e += 1;

433

434
435 | }
436 | #pragma v e ct o r =TIMER1 A0 VECTOR
437 | i n t e r r u p t v o i d Timer A0 ( v o i d )
438 | {
439 | P1IE |= BIT1 ; / / Enable i n t e r r u p t again .
440 | }
Scratch Sumo-Bot: Tracking a Moving Object | 22

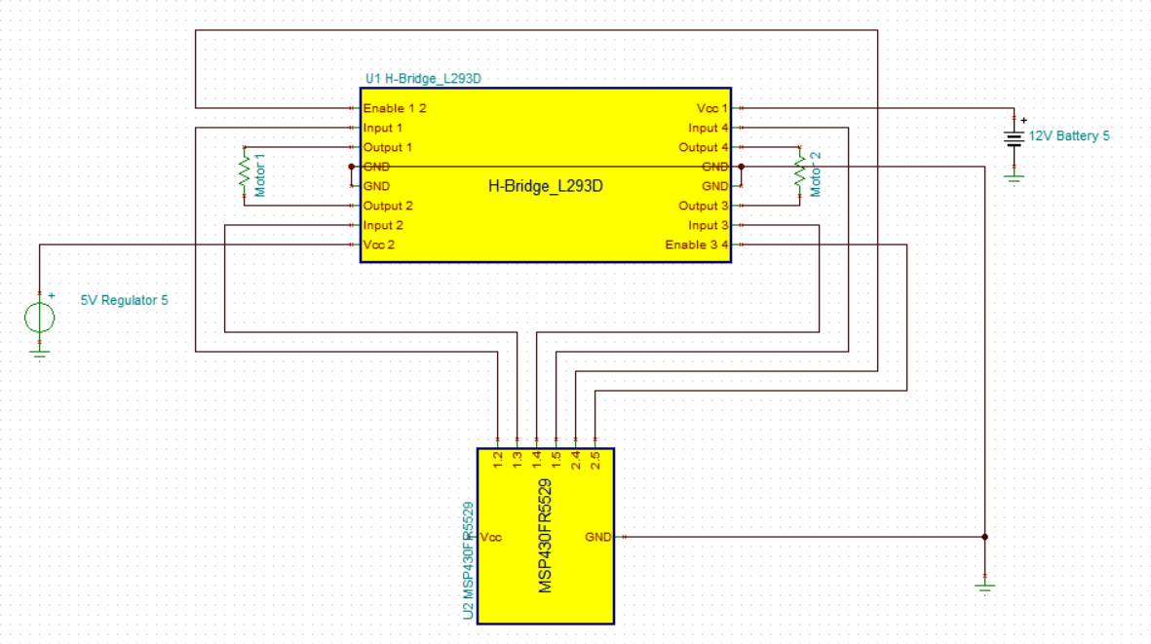
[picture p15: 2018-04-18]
Final Project Pictures/H_Bridge_Schematic.png

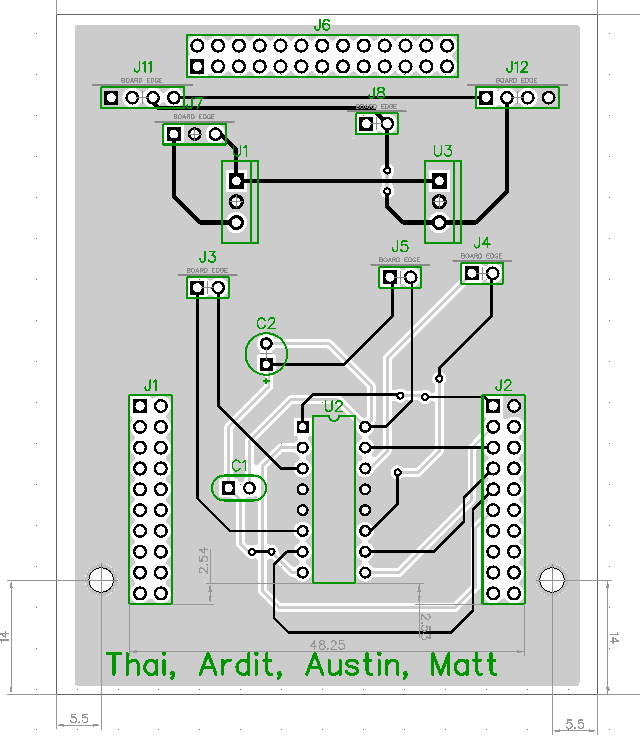
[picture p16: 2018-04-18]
Final Project Pictures/PCB.png

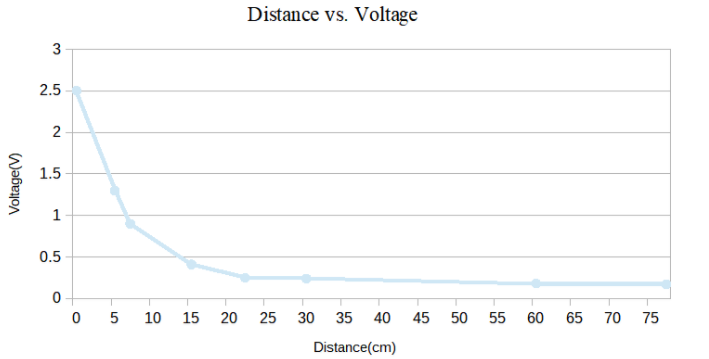
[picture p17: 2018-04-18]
Final Project Pictures/Distance Vs. Voltage.png

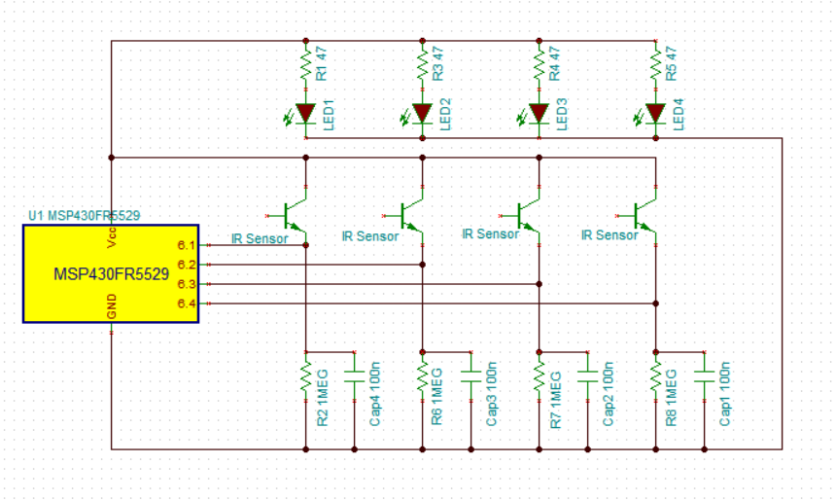
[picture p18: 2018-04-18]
Final Project Pictures/New irs.png

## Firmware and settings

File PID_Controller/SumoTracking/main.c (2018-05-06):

#include <msp430.h> 
//for averaging ADC values
int adc3 = 0;
int adc4 = 0;
int buf3[10];
int buf4[10];
unsigned int index;

int Kp=3;
int Kd=0;
int Ki=0;
int error3 = 0;
int error4 = 0;
int error3Prev = 0;
int error4Prev = 0;
int proportional3 = 0;
int proportional4 = 0;
int derivative3 = 0;
int derivative4 = 0;
int accumulator3 = 0;
int accumulator4 = 0;
int integral3 = 0;
int integral4 = 0;
int pid3 = 0;
int pid4 = 0;
int tempLeft = 0;
int tempRight = 0;
int adc_out=0;
int scale_value = 8;

int control_type = 0;
int flag = 0;
int desired = 0; //ADC value
void PWMInit(void);
void sensing(void);
void starting(void);
void setMotor();
void ADCInit(void);
void updatePID(void);
void distToADC(int distance);
void setScaledMotor(int left, int right);
void pinInit(void);


/**
 * main.c
 */
int main(void)
{
    // Stop watchdog timer
    WDTCTL = WDTPW | WDTHOLD;

    // Initialization
    pinInit();
    PWMInit();
    ADCInit();

    // Reset the speed of both motors
    setMotor(0,0);

    /*
    *   Compute desired value in ADC
    *   Max: 200 (closest)
    *   Min: 100 (furthest
    *
    *   desired = 200;
    */

    // Desired trailing distance
    int distance = 5; // in centimeters
    distToADC(distance); // Distance to ADC value

    // Sumo-bot constantly sense the environment
    while(1) //inifite loop
    {
        sensing();
    }
}


void starting(void)
{
    sensing();
}

/*
 * Enable the ADC converter to start sensing the environment
 * This function is called in main
 */
void sensing(void)
{
    ADC12CTL0 |= ADC12ENC;       // ADC12 enabled
    ADC12CTL0 |= ADC12SC;        // Start sampling/conversion
    __bis_SR_register(GIE);     // LPM0, ADC12_ISR will force exit

}

/*
 * Proportional - Integral - Derivative Controller of the robot
 * Is called in the Interrupt
 */
void updatePID(void){
    // Calculating the Error term
    error3Prev = error3; // Right motor
    error4Prev = error4; // Left motor
    error3 = desired - adc3;
    error4 = desired - adc4;

    // Calculating the Proportional term
    proportional3 = Kp * error3; // Right motor
    proportional4 = Kp * error4; // Left motor

    // Calculating the Derivative term
    derivative3 = Kd * (error3Prev-error3); // Right motor
    derivative4 = Kd * (error4Prev-error4); // Ledt motor

    // Calculating the accumulator for the Error term
    accumulator3 = accumulator3 += error3;
    accumulator4 = accumulator4 += error4;

    // Capping accumulator values
    if(accumulator3>50){ // Right motor
        accumulator3 = 50;
    }else if(accumulator3<-50){
        accumulator3 = -50;
    }

    if(accumulator4>50){  // Left motor
        accumulator4 = 50;
    }else if(accumulator4<-50){
        accumulator4 = -50;
    }

    // Calculating the Integral term
    integral3 = Ki * accumulator3; // Right motor
    integral4 = Ki * accumulator4; // Left motor

    // Adding the Proportional - Integral - Derivative temrs
    // up to create the PID controller
    pid3 = proportional3+integral3-derivative3;
    pid4 = proportional4+integral4-derivative4;

    //convert pid range to PWM range
    setScaledMotor(pid3,pid4);
}

/*
 * This function scale the PWM range, since the left motor is
 * slightly stronger than the right motor, making the robot
 * steer right.
 */
void setScaledMotor(int left, int right){
    //left limit -999 to 999
    //right limit -870 to 870
    //expected range -200 to 200
    tempLeft = (left*5/2)*scale_value;
    tempRight = ((right*9)/4)*scale_value;

    // 30 is minimum value (furthest)
    if (tempLeft < 30 && tempLeft > 0){
        tempLeft = 30;
    }
    if(tempRight < 30 && tempRight > 0){
        tempRight = 30;
    }

    if (tempLeft > -30 && tempLeft < 0){
        tempLeft = -30;
    }
    if(tempRight > -30 && tempRight < 0){
        tempRight = -30;
    }
    // 999 is maximum value (closest)
    if(tempLeft< -999){
        tempLeft = -999;
    }
    if(tempRight< -999){
        tempRight = -999;
    }

    if (tempLeft>999){
        tempLeft = 999;
    }
    if (tempRight>870){
        tempRight = 870;
    }
    //       Right      Left
    setMotor(tempLeft, tempRight);

}

/*
 * This function set the PWM value of the
 * two motors, hence control their speed
 */
void setMotor(int left, int right)
{
    if(right < 0) //Backwards, clock-wise
    {
        P2OUT |= BIT5; //Sets direction for H-bridge
        TA0CCR3 = (left * -1); //Speed of the motor CCR/1000
    }
    else if(right == 0) //stopping
    {
        TA0CCR3 = 0;
    }
    else //Forwards, counter clock-wise
    {
        P2OUT &= ~BIT5; //Sets direction for H-bridge
        TA0CCR3 = left; //Speed of the motor CCR/1000
    }

    if(left < 0)
    {
        P1OUT |= BIT5;
        TA2CCR1 = (right * -1);
    }
    else if(left == 0)
    {
        TA2CCR1 = 0;
    }
    else // forwards, clock-wise
    {
        P1OUT &= ~BIT5;
        TA2CCR1 = right;
    }
}

/*
 * Characterization code for the system
 * Convert the desired distance to ADC value
 * Using piece-wise functions
 */
void distToADC(int distance){
    // 0cm to 7cm range
    if (distance >= 0 && distance <= 7){
        adc_out = distance*-53.6 + 492.8;
    // 7cm to 12cm range
    } else if (distance > 7 && distance <= 12){
        adc_out = distance*-13.689 + 215.54;
    // 12cm to 30cm range
    } else if (distance > 12 && distance  <= 30){
        adc_out = distance*-1.8716 + 74.838;
    }
    // Default value
    else{
        adc_out = 290;
    }
}
void pinInit(void){
    P2DIR |= BIT0;  // Pin 2.0 initialization
    P2OUT |= BIT0;

    P2DIR |= BIT2;  // Pin 2.2 initialization
    P2OUT |= BIT2;

    P2DIR |= BIT5;
    P1DIR |= BIT5;

    P1SEL =0; //Select GPIO option
    P1DIR |=BIT0; //set Port 1.0 output ---LED
    P1OUT &= ~BIT0;  // LED OFF

    P4SEL =0; //Select GPIO option
    P4DIR |=BIT7; //set Port 4.7 output ---LED
    P4OUT &= ~BIT7;  // LED OFF

    P1DIR &=~(BIT1); //set Port 1.1 input --- pushbutton
    P1REN|=BIT1;//enable pull-up/pull-down resistor on
    P1OUT|=BIT1; //choose the pull-up resistor

    P1IE |=BIT1;//enable the interrupt on Port 1.1
    P1IES |=BIT1;//set as falling edge
    P1IFG &=~(BIT1);//clear interrupt flag
}
void PWMInit(void)
{
    P1DIR |= BIT4;      // Initialize PWM to output on P1.4
    P1SEL |= BIT4;

    P2DIR |= BIT4;      // Initialize PWM to output on P2.4
    P2SEL |= BIT4;

    TA0CCR0 =1000-1;
    TA2CCR0 =1000-1;
    TA0CCTL3 =OUTMOD_7;
    TA0CCR3 =999;
    TA2CCTL1 =OUTMOD_7;
    TA2CCR1 = 999;
    TA0CTL = TASSEL_2 + MC_1 + TACLR;
    TA2CTL = TASSEL_2 + MC_1 + TACLR;
}

void ADCInit(void)
{
    ADC12CTL0 = ADC12ON+ADC12MSC+ADC12SHT02; // Turn on ADC12, set sampling time
    ADC12CTL1 = ADC12SHP+ADC12CONSEQ_1;       // Use sampling timer, single sequence
    ADC12MCTL0 = ADC12INCH_0;                 // ref+=AVcc, channel = A0
    ADC12MCTL1 = ADC12INCH_1;                 // ref+=AVcc, channel = A1
    ADC12MCTL2 = ADC12INCH_2;                 // ref+=AVcc, channel = A2
    ADC12MCTL3 = ADC12INCH_3;
    ADC12MCTL4 = ADC12INCH_4 + ADC12EOS;        // ref+=AVcc, channel = A3, end seq.
    ADC12IE = 0x10;                           // Enable ADC12IFG.3
    ADC12CTL0 |= ADC12ENC;                    // Enable conversions
    /*Sets ADC Pin to NOT GPIO*/
    P6SEL |= BIT1 + BIT2 + BIT3 + BIT4;                            // P6.0 ADC option select
    P6DIR &= ~(BIT1 + BIT2 + BIT3 + BIT4);
    P6REN |= BIT1 + BIT2 + BIT3 + BIT4;
    P6OUT &= ~(BIT1 + BIT2 + BIT3 + BIT4);
    ADC12CTL0 |= ADC12ENC;
    ADC12CTL0 |= ADC12SC;
}

#if defined(__TI_COMPILER_VERSION__) || defined(__IAR_SYSTEMS_ICC__)
#pragma vector = ADC12_VECTOR
__interrupt void ADC12_ISR(void)
#elif defined(__GNUC__)
void __attribute__ ((interrupt(ADC12_VECTOR))) ADC12_ISR (void)
#else
#error Compiler not supported!
#endif
{

    switch(__even_in_range(ADC12IV,34))
    {
    case  0: break;                           // Vector  0:  No interrupt
    case  2: break;                           // Vector  2:  ADC overflow
    case  4: break;                           // Vector  4:  ADC timing overflow
    case  6: break;                                  // Vector  6:  ADC12IFG0
    case  8:break;                           // Vector  8:  ADC12IFG1
    case 10: break;                           // Vector 10:  ADC12IFG2
    case 12:break;                           // Vector 12:  ADC12IFG3
    case 14:
        // For every 10 ADC samples, we use 1 for stability of the system
        if(index < 10){     //adds new value to array for average of 10
            buf3[index] = ADC12MEM3; // buffer for right motor
            buf4[index] = ADC12MEM4;
            index++;
        }
        else{     //computes average of 10 and transmits value; resets array index
            long average3 = 0;
            long average4 = 0;
            int i = 0;
            for(i = 0; i < 10 ; i ++){
                average3 += buf3[i];
                average4 += buf4[i];
            }
            average3 /= 10;
            average4 /= 10;
            index=0;
            flag=1;
            // -120 for Full vs Weak
            adc3 = average3 ; //changes duty cycle
            adc4 = average4 ; //changes duty cycle

            // Calling the PID controller function
            updatePID();
        }

        __bic_SR_register_on_exit(LPM0_bits);
        break;                           // Vector 14:  ADC12IFG4
    case 16: break;                           // Vector 16:  ADC12IFG5
    case 18: break;                           // Vector 18:  ADC12IFG6
    case 20: break;                           // Vector 20:  ADC12IFG7
    case 22: break;                           // Vector 22:  ADC12IFG8
    case 24: break;                           // Vector 24:  ADC12IFG9
    case 26: break;                           // Vector 26:  ADC12IFG10
    case 28: break;                           // Vector 28:  ADC12IFG11
    case 30: break;                           // Vector 30:  ADC12IFG12
    case 32: break;                           // Vector 32:  ADC12IFG13
    case 34: break;                           // Vector 34:  ADC12IFG14
    default: break;
    }
}

/*
 * Button Interrupt that control the Controller Type of the robot
 * There are 4 modes in total: only Proportional, Proportional-Integral,
 * Proportional-Derivative, and all Proportional-Integral-Derivative
 */
#pragma vector=PORT1_VECTOR
__interrupt void PORT_1(void)
{
    P1IE &= ~BIT1; // Disable interrupt

    //Debounce 1
    __delay_cycles(1);

    //Debounce 2
    TA1CTL = TASSEL_1 + MC_1 + ID_1; //Set up Timer A, Count up, divider 2
    TA1CCTL0 = 0x10; // Set up compare mode for CCTL
    TA1CCR0 = 2000; // Duration at which the interrupt is disable
                    // Duration 2000/16kHz = 1/8 sec.
    P1IFG &=~(BIT1); // Clear flag

    // Loop back to control type 0
    if (control_type > 3){
        control_type = 0;
    }

    switch(control_type){
    case 0: //Only PI
        P4OUT |= BIT7; // Turn 4.7 on for 01
        P1OUT &= ~BIT0; // Turn 1.0 on
        Ki =1;
        scale_value = 5;
        break;
    case 1: // PD
        P1OUT |= BIT0; // Turn 1.0 on for 10
        P4OUT &= ~BIT7; // Turn 4.7 off
        Ki = 0;
        Kd = 1;
        scale_value = 8;
        break;
    case 2: //PID
        P4OUT |= BIT7; // Turn 4.7 on for 11
        P1OUT |= BIT0; // Turn 1.0 on for
        Ki = 1;
        Kd = 1;
        scale_value = 1;
        break;
    case 3: //Only P
        P4OUT &= ~BIT7; // Turn 4.7 on for 11
        P1OUT &= ~BIT0; // Turn 1.0 on for
        Ki = 0;
        Kd = 0;
        scale_value = 8;
        break;
    default:
        break;
    }
    control_type += 1;


}
#pragma vector=TIMER1_A0_VECTOR
__interrupt void Timer_A0(void)
{
    P1IE |= BIT1; //Enable interrupt again.
}

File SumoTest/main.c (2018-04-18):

//MattttttttLawrence
#include <msp430.h>

//Initialize Sensor Thresholds.
const int PHOTORESISTOR_THRESH1 = 200;
const int PHOTORESISTOR_THRESH2 = 200;
const int IRSENSOR_THRESH1 = 40;
const int IRSENSOR_THRESH2 = 40;
int sensorThreshHolds[4] = {PHOTORESISTOR_THRESH1, PHOTORESISTOR_THRESH2, IRSENSOR_THRESH1, IRSENSOR_THRESH2};

//Initialize Speed constants and turn duration.
int MAX = 999;
int TURN_SPEED = 999;
unsigned int TURN_TIME = 500000;
int attackSpeedLeft, attackSpeedRight;

//Initialize variable that the program can read to see sensor values.
int adc_value[4] = {0,0,0,0};

//define button and variables for UART remote control mode.
#define BUTTON BIT0;
int fightMode = -1;
int direction = 0;

void attack();
void backAway();
int sensorCheck();
int setSensor();
int readSensor();
void standBy();

void ADCInit(void)
{

    /*Configure ADC*/
    /*ADC12CTL0 = ADC12SHT02 + ADC12ON;         // Sampling time, ADC12 on
    ADC12CTL1 =  ADC12CSTARTADD_1 + ADC12SHP + ADC12CONSEQ_1;                     // Use sampling timer
    ADC12CTL0 |= BIT4 + BIT5 + BIT6;
    ADC12MCTL1 = ADC12INCH_1;
    ADC12MCTL2 = ADC12INCH_2;
    ADC12MCTL3 = ADC12INCH_3;
    ADC12MCTL4 = ADC12INCH_4 + ADC12EOS;
    ADC12IE |= BIT1 + BIT2 + BIT3 + BIT4;                           // Enable interrupt
    ADC12CTL0 |= ADC12ENC;*/
    ADC12CTL0 = ADC12ON+ADC12MSC+ADC12SHT02; // Turn on ADC12, set sampling time
    ADC12CTL1 = ADC12SHP+ADC12CONSEQ_1;       // Use sampling timer, single sequence
    ADC12MCTL0 = ADC12INCH_0;                 // ref+=AVcc, channel = A0
    ADC12MCTL1 = ADC12INCH_1;                 // ref+=AVcc, channel = A1
    ADC12MCTL2 = ADC12INCH_2;                 // ref+=AVcc, channel = A2
    ADC12MCTL3 = ADC12INCH_3;
    ADC12MCTL4 = ADC12INCH_4 + ADC12EOS;        // ref+=AVcc, channel = A3, end seq.
    ADC12IE = 0x10;                           // Enable ADC12IFG.3
    ADC12CTL0 |= ADC12ENC;                    // Enable conversions
    /*Sets ADC Pin to NOT GPIO*/
    P6SEL |= BIT1 + BIT2 + BIT3 + BIT4;                            // P6.0 ADC option select
    P6DIR &= ~(BIT1 + BIT2 + BIT3 + BIT4);
    P6REN |= BIT1 + BIT2 + BIT3 + BIT4;
    P6OUT &= ~(BIT1 + BIT2 + BIT3 + BIT4);
}

void UARTInit(void)
{
    /*Configures UART*/
    P3SEL |= BIT3;          // UART TX
    P3SEL |= BIT4;          // UART RX
    UCA0CTL1 |= UCSWRST;    // Resets state machine
    UCA0CTL1 |= UCSSEL_2;   // SMCLK
    UCA0BR0 = 6;            // 9600 Baud Rate
    UCA0BR1 = 0;            // 9600 Baud Rate
    UCA0MCTL |= UCBRS_0;    // Modulation
    UCA0MCTL |= UCBRF_13;   // Modulation
    UCA0MCTL |= UCOS16;     // Modulation
    UCA0CTL1 &= ~UCSWRST;   // Initializes the state machine
    UCA0IE |= UCRXIE;
}

void pinInit(void)
{
    P1DIR |= BIT2 + BIT3 + BIT4 + BIT5; // for motors
    P1DIR &= ~BIT0;                            // Set P1.0 to output direction
    P1OUT &= ~BIT0;

    P1REN |= BIT1;                            // Enable P1.1 internal resistance
    P1OUT |= BIT1;                            // Set P1.1 as pull-Up resistance
    P1IES &= ~BIT1;                           // P1.1 Lo/Hi edge
    P1IFG &= ~BIT1;                           // P1.1 IFG cleared
    P1IE |= BIT1;                             // P1.1 interrupt enabled
}

void timerInit(void)
{
    P2DIR |= BIT4+BIT5;                       // P1.2 and P1.3 output for motors
    P2SEL |= BIT4+BIT5;                       // P1.2 and P1.3 options select for motors
    TA2CCR0 = 1000 - 1;                          // PWM Period
    TA2CCTL1 = OUTMOD_7;                      // CCR1 reset/set
    TA2CCR1 = 384;                            // CCR1 PWM duty cycle
    TA2CCTL2 = OUTMOD_7;                      // CCR2 reset/set
    TA2CCR2 = 128;                            // CCR2 PWM duty cycle
    TA2CTL = TASSEL_2 + MC_1 + TACLR;         // SMCLK, up mode, clear TAR
}

void motorPWM(int left, int right)
//'left' and 'right' are the input speed
{
    if(left < 0) //backwards, clock-wise
    {
        P1OUT &= ~BIT4;
        P1OUT |= BIT5; // Sets direction for H-bridge
        TA2CCR2 = (left * -1);//Speed of motor CCR/1000
    }
    else if(left == 0) //stopping
    {
        P1OUT &= ~BIT4;
        P1OUT &= ~BIT5;// Sets direction for H-bridge
        TA2CCR2 = 0;//Speed of motor CCR/1000
    }
    else // forwards, counter clock-wise
    {
        P1OUT |= BIT4;
        P1OUT &= ~BIT5;// Sets direction for H-bridge
        TA2CCR2 = left;//Speed of motor CCR/1000
    }

    if(right < 0) //backwards, counter clock-wise
    {

        P1OUT &= ~BIT2;
        P1OUT |= BIT3; // Sets direction for H-bridge
        TA2CCR1 = (right * -1);//Speed of motor CCR/1000
    }
    else if(right == 0) //stopping
    {
        P1OUT &= ~BIT2;
        P1OUT &= ~BIT3;// Sets direction for H-bridge
        TA2CCR1 = 0;//Speed of motor CCR/1000
    }
    else // forwards, clock-wise
    {
        P1OUT |= BIT2;
        P1OUT &= ~BIT3;// Sets direction for H-bridge

        TA2CCR1 = right;
    }
}


// Get the ADC value using ADC interrupt
int readSensor(int SensorToRead)
{
    __delay_cycles(10000);
    ADC12CTL0 |= ADC12ENC;
    ADC12CTL0 |= ADC12SC;                   // Start sampling/conversion
    __bis_SR_register(LPM4_bits + GIE);     // LPM0, ADC12_ISR will force exit


    return adc_value[SensorToRead];
}

// Check the status of all 4 sensors
int sensorCheck()
{
    if(readSensor(0) > sensorThreshHolds[0])
    {
        return 0;
    }
    else if(readSensor(1) > sensorThreshHolds[1])
    {
        return 1;
    }
    else if(readSensor(2) > sensorThreshHolds[2])
    {
        return 2;
    }
    else if(readSensor(3) > sensorThreshHolds[3])
    {
        return 3;
    }



    return -1;
}

// Attach strategy for the robot
void attack()
{
    int attackSpeedLeft = 0, attackSpeedRight = 0; //Initialize attack speed
    int sensorValue = sensorCheck(); // Check each sensor's value
    if(sensorValue == -1) // If there is no significant changes, do nothing
        return;
    else if(sensorValue == 0 || sensorValue == 1) // The sensors on the bottom
    {
        backAway(sensorValue); //Back the bot away
        return;
    }
    else if(sensorValue == 2 || sensorValue == 3) // The sensors on the top
    {
        attackSpeedLeft = MAX;
        attackSpeedRight = MAX;
    }
    // Call motorPWM mode to tell how the robot should move
    motorPWM(attackSpeedLeft,attackSpeedRight);
}

// Back the robot away if it on the edge of the Dojo
void backAway(int leftOrRight)
{
    motorPWM(-999, -999);
    __delay_cycles(300000);
    // Choose which way to turn
    switch(leftOrRight)
    {
    case 0: // Left
        motorPWM(999, -999);
        break;
    case 1: // Right
        motorPWM(-999, 999);
        break;
    }



    // How long the robot's going turning for
    __delay_cycles(1000000);


    motorPWM(999, 999);
    __delay_cycles(500000);

    // How long the robot's going to go forward before going
    // into stand-by mode.

}
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
